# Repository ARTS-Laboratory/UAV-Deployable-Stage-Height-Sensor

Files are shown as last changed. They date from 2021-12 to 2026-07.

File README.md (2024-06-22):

# UAV-Deployable-Stage-Height-Sensor
UAV Deployable Stage Height Sensor with Electro-permanent Magnet Docking Mechanism

<p align="center">
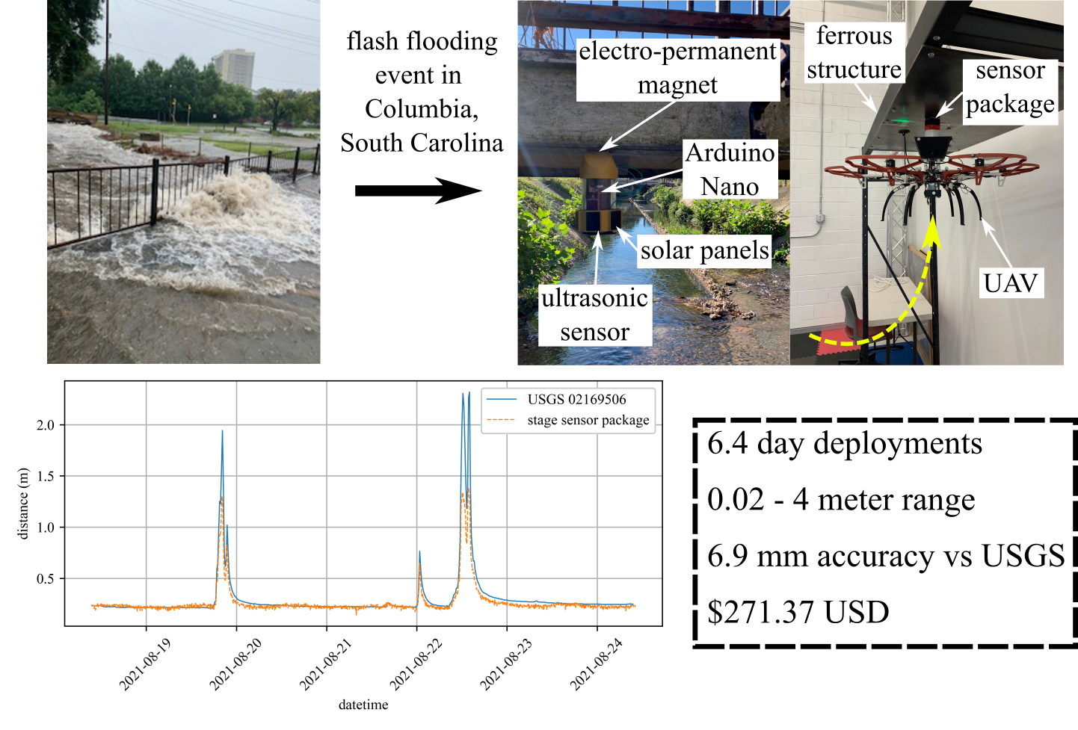
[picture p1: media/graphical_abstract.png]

</p>
<p align="center">
Figure 1: Drone delivering a sensor package underneath a structure.
</p>

## V0
1. Data logging saved onto SD card
2. Battery monitoring
3. Solar load sharing
4. Measures stage, temperature, pressure, humidity
5. EPM with wireless toggling to attach under structures

## V1 (projected)
1. Adaptive sampling algorithm
2. Wireless data transfer with GUI
3. Camera integration

## Licensing and Citation

[][cc-by-sa]

This work is licensed under a
[Creative Commons Attribution-ShareAlike 4.0 International License][cc-by-sa].

[cc-by-sa]: http://creativecommons.org/licenses/by-sa/4.0/
[cc-by-sa-image]: https://licensebuttons.net/l/by-sa/4.0/88x31.png
[cc-by-sa-shield]: https://img.shields.io/badge/License-CC%20BY--SA%204.0-lightgrey.svg

Cite as:

@Misc{ARTSLabUavDeployableStage,     
  author = {{ARTS-L}ab},  
  howpublished = {GitHub},  
  title  = {{UAV} Deployable Stage Height Sensor}, 
  groups = {{ARTS-L}ab},    
  url    = {https://github.com/ARTS-Laboratory/UAV-Deployable-Stage-Height-Sensor},   
}

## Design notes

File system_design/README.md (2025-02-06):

# System Design
Hardware variations named after coastal towns and cities in South Carolina

## Georgetown
Battery-powered ultrasonic sensor

## Charleston
Battery and solar panel-powered ultrasonic sensor

## Beaufort
Wireless communication in addition to battery and solar panel-powered ultrasonic sensor

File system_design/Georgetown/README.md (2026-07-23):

# Georgetown
UAV deployable sensor package for measuring water height. This document lists the updates made to the sensor pacakge over time.
## V0.1
1. Oldest version
2. Basic datalogger setup with modular RTC and SD card
3. Accelerometer integrated into daughter board

## V0.2
1. Teensy 4.0 microcontroller
2. Added environmental sensor

## V0.3
1. Teensy 4.0 or Arduino Nano microcontroller
2. Added DC current sensor

## V0.4
1. Arduino Nano microcontroller
2. Magnet power control circuit on daughter board
3. No accelerometer on daughter board
4. Solar panel load sharing on daughter board

## V0.5
1. Major CAD and PCB update from V0.4
2. Microcontroller : Arduino Nano
3. Solar panels moved to the bottom of the sensor package
4. BMS added to manage solar load sharing in main PCB, daughter PCB eliminated
5. Uses dynamic sleep interval depending on battery voltage level
6. Uses permanent magnet to attach to steel structures
7. Easy sliding water-proof clear tube

## V0.5.1
1. Minor design updates in PCB from V0.5.

## V0.5.2 (present version)
1. Major power electronics update from V0.5.1
2. Uses Mosfet based switching to turn off device during sleep. Wakes up using RTC interrupt. Resulting in very low power consumption and longer deployment time.
3. Sensing features: Water level distance from sensor, Humidity, temperature, pressure, battery voltage (recorded against RTC time)

## V0.6 (Proposed)
1.  Back to being UAV deployable using [this system](https://github.com/ARTS-Laboratory/UAV-Understructure-Sensor-Deployment-and-Recovery-System).
2. Uses module that has [single ultra sound transducer](https://cdn.shopify.com/s/files/1/0550/8091/0899/files/11832.pdf?v=1726578772) to lower current consumption.

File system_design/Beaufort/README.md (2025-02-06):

# Beaufort
Wireless communication in addition to battery and solar panel-powered ultrasonic sensor

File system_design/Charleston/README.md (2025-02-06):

# Charleston
Battery and solar panel-powered ultrasonic sensor

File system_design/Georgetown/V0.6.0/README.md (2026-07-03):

# UAV Rapidly-Deployable Stage Sensor with Permanent Magnet Docking Mechanism for Flood Monitoring in Undersampled Watersheds
## Deployment note
* Do not plug or unplug the SD card while power is on. Swtich must be turned to the off position to plug/unplug the SD card. 
## Fully assembled sensor package
<p align="center">

</p>

## System diagram
<p align="center">

</p>

## V0.5 PCB Top side
<p align="center">

</p>

## V0.5 PCB Bottom side
<p align="center">

</p>

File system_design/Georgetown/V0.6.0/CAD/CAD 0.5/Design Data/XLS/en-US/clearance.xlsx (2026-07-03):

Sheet: Ansi Unified Screw Threads
I | Sort Order -1
Fastener Type | Size | Shaft Diameters |  |  | Head Dimensions
 |  | Close | Normal | Loose | Diameter | Depth/Angle | Head Type
Flat Head Machine Screw (82) | #0 | 0.0635 | 0.07 | 0.073 | 0.119 | 82 | 2
Flat Head Machine Screw (82) | #1 | 0.076 | 0.081 | 0.089 | 0.146 | 82 | 2
Flat Head Machine Screw (82) | #2 | 0.089 | 0.096 | 0.1065 | 0.172 | 82 | 2
Flat Head Machine Screw (82) | #3 | 0.104 | 0.11 | 0.12 | 0.199 | 82 | 2
Flat Head Machine Screw (82) | #4 | 0.116 | 0.1285 | 0.136 | 0.225 | 82 | 2
Flat Head Machine Screw (82) | #5 | 0.1285 | 0.136 | 0.154 | 0.252 | 82 | 2
Flat Head Machine Screw (82) | #6 | 0.144 | 0.1495 | 0.1695 | 0.279 | 82 | 2
Flat Head Machine Screw (82) | #8 | 0.1695 | 0.177 | 0.1935 | 0.332 | 82 | 2
Flat Head Machine Screw (82) | #10 | 0.196 | 0.201 | 0.221 | 0.385 | 82 | 2
Flat Head Machine Screw (82) | #12 | 0.221 | 0.228 | 0.246 | 0.438 | 82 | 2
Flat Head Machine Screw (82) | 1/4 | 0.257 | 0.266 | 0.2812 | 0.507 | 82 | 2
Flat Head Machine Screw (82) | 5/16 | 0.323 | 0.332 | 0.3437 | 0.635 | 82 | 2
Flat Head Machine Screw (82) | 3/8 | 0.386 | 0.397 | 0.4062 | 0.762 | 82 | 2
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

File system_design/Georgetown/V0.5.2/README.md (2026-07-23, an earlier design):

# UAV Rapidly-Deployable Stage Sensor with Permanent Magnet Docking Mechanism for Flood Monitoring in Undersampled Watersheds
## Deployment note
* Do not plug or unplug the SD card while power is on. Swtich must be turned to the off position to plug/unplug the SD card. 
## Fully assembled sensor package
<p align="center">

</p>

## System diagram
<p align="center">
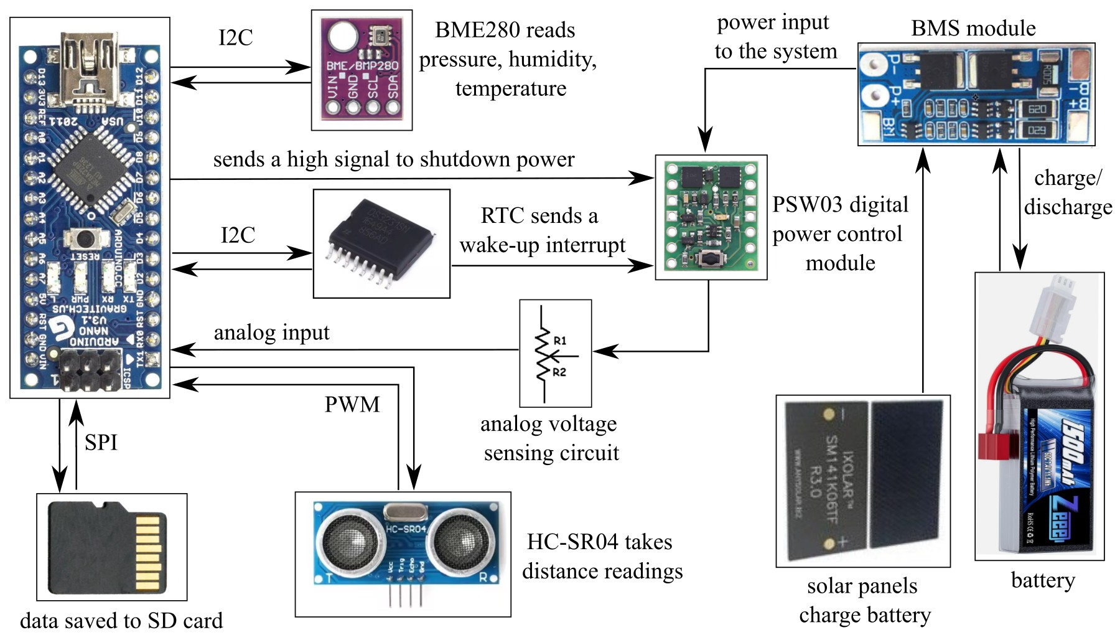
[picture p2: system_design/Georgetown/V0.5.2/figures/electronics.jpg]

</p>

## V0.5 PCB Top side
<p align="center">

</p>

## V0.5 PCB Bottom side
<p align="center">

</p>

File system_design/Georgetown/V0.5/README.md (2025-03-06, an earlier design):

# UAV Rapidly-Deployable Stage Sensor with Permanent Magnet Docking Mechanism for Flood Monitoring in Undersampled Watersheds

<p align="center">
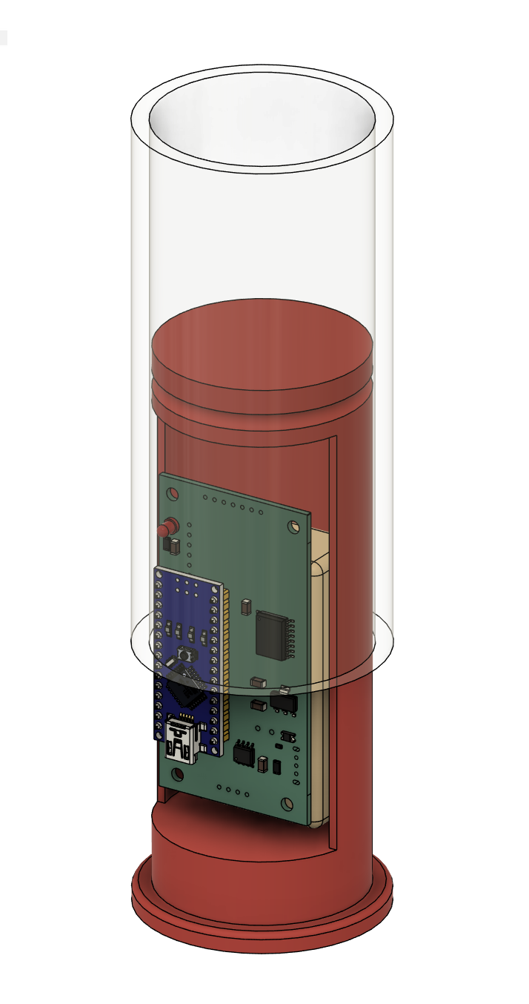
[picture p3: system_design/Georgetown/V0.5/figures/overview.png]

</p>

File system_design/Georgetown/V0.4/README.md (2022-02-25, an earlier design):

# UAV Rapidly-Deployable Stage Sensor with Electro-permanent Magnet Docking Mechanism for Flood Monitoring in Undersampled Watersheds

<p align="center">

</p>

## bill of materials
A complete bill of materials, with specifications for the base package, solar add-on module, and EPM add-on module

## CAD
STL and F3D files of 3D printed parts 

## code
Calibration and data collection codes

## EDA
KiCAD schematics and PCB layouts of main and daughter boards

## figures
SVG and PDF files of all figures presented in the work

## testing_data
Data from benchtop and field tests

## data_headers.csv
Example data headers for csv file generated by data_collection.ino

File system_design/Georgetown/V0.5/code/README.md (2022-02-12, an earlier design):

## clock_calibration
- calibrates the DS3231 to compiling time or a user defined time

## data_collection
- main program for base package with serial communication

## EPM_data_collection
- main program for EPM package acting as receiver

## magnet_toggle
- uses serial commands to toggle EPM on and off

## rf_controller
- configures a transmitter for the package with the RF controller PCB

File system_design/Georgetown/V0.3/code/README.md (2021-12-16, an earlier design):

## USS5_x
1. Compatible with Arduino Nano only

## USS5_asa
1. Sensor code with adaptive sampling algorithm integrated

## USS5_seconds
1. Sensor code with fixed 5 second intervals of sleep, used for debugging

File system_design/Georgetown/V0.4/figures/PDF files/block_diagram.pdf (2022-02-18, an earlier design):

MCU
Arduino
Nano

real-time
clock
DS3231

Li+
coin cell

ultrasonic sensor
HCSR04

onboard
memory
micro SD

wireless
communication
nRF24L01+
electropermanet
magnet
EPM V3 R5C

environmental
sensor
BME280

5V
regulator

current sensor
INA219

LiPo battery
Socokin 7.4V 1500 mAH

magnet power
control circuit

I2C

SPI

PWM

daughter board

main board

PWM

interrupt

interrupt

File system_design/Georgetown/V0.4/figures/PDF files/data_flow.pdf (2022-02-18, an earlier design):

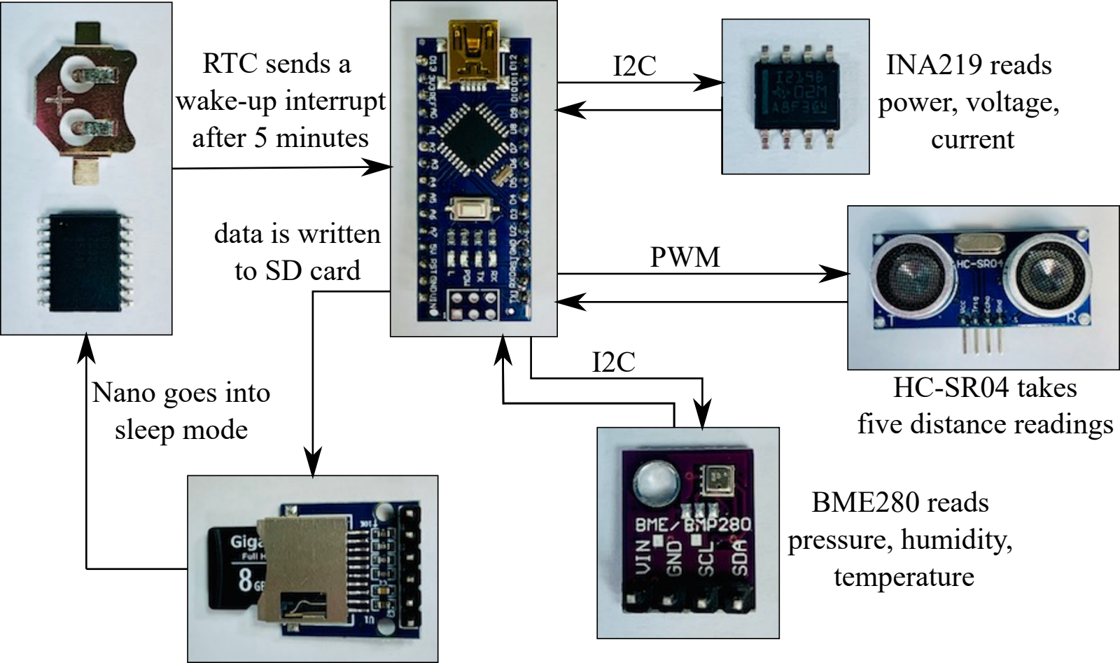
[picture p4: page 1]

RTC sends a
wake-up interrupt
after 5 minutes

INA219 reads
power, voltage,
current

HC-SR04 takes
five distance readings

BME280 reads
pressure, humidity,
temperature

data is written
to SD card

Nano goes into
sleep mode

I2C

PWM

I2C

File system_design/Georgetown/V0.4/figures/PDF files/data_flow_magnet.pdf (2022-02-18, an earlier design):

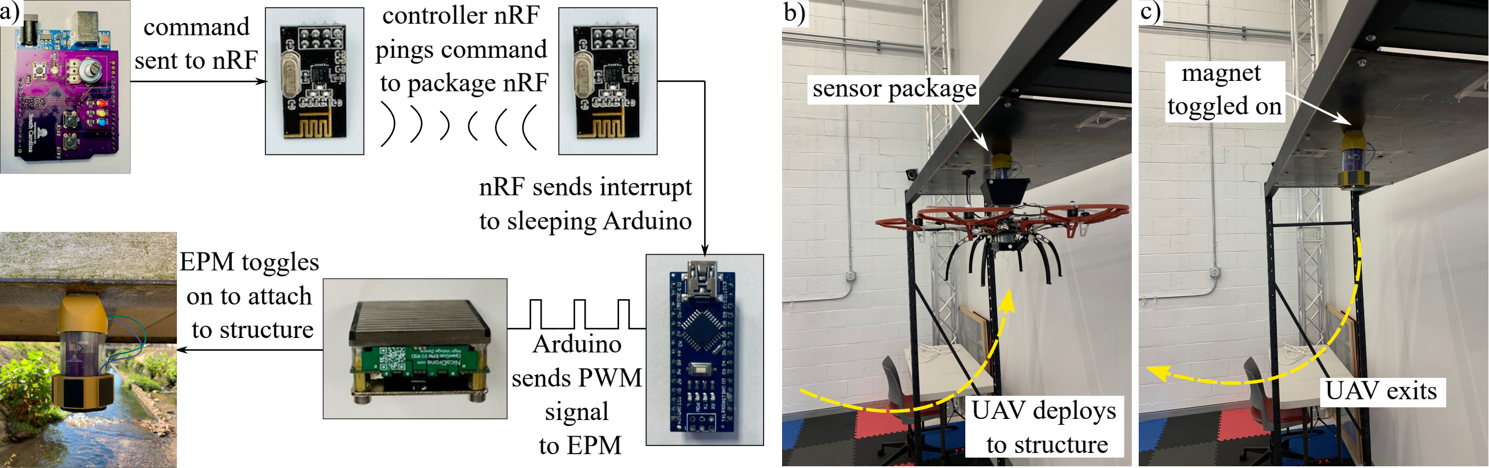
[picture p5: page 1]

command
sent to nRF

EPM toggles
on to attach
to structure | Arduino
| sends PWM
| signal
| to EPM

nRF sends interrupt
to sleeping Arduino

controller nRF
pings command
to package nRF

UAV exits

magnet
toggled on

UAV deploys
to structure

sensor package

a) | b) | c)

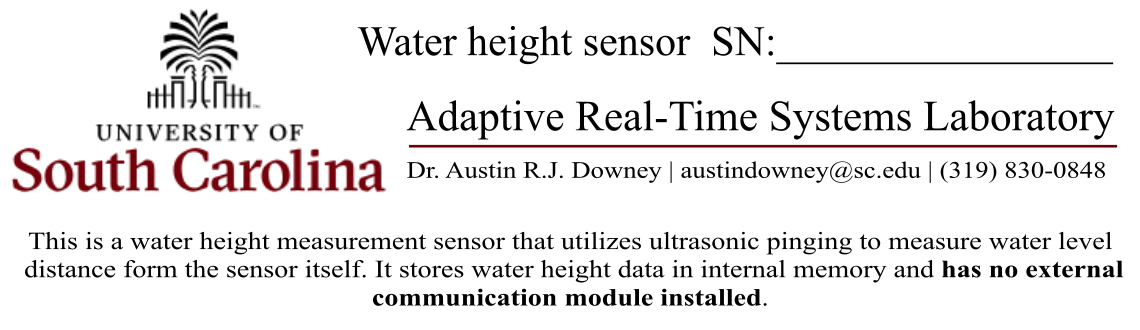
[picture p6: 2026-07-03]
system_design/Georgetown/V0.6.0/Sticker label/USC label.png

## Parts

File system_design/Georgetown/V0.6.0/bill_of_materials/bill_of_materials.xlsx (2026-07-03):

Designator | Component | Amount | Individual Cost | Total Cost | Vendor 1 | Vendor 2 | Vendor 3 | Vendor 4 | Vendor 5 | Vendor 6
Arduino Nano | Arduino Nano | 1 | 25.7 | 25.7 | https://store-usa.arduino.cc/products/arduino-nano?gad_source=1 | https://www.digikey.com/en/products/detail/arduino/A000005/2638989?gclsrc=aw.ds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 | https://www.ebay.com/itm/254630577493?chn=ps&google_free_listing_action=view_item&gQT=2
Micro SD card slot/tray | 112J-TDAR-R01 | 1 | 2.52 | 2.52 | https://www.digikey.com/en/products/detail/attend-technology/112J-TDAR-R01/17634680 | https://www.ebay.com/itm/235081679206?chn=ps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
NRF24L01+ | NRF24L01+ 2.4GHz Wireless RF Transceiver Module | 1 | 1.4 | 1.4 | https://www.amazon.com/Makerfire-Arduino-NRF24L01-Wireless-Transceiver/dp/B00O9O868G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 | https://www.digikey.com/en/products/detail/ai-thinker/NF-01-S/16688873?gclsrc=aw.ds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 | https://www.ebay.com/itm/185777140664?itmmeta=01JXJF02RJ2SD81DKBZE32WGPJ
DS3231 real-time clock | DS3231M+ | 1 | 11.96 | 11.96 | https://www.digikey.com/en/products/detail/analog-devices-inc-maxim-integrated/DS3231M/2402420 | https://www.mouser.com/ProductDetail/Analog-Devices-Maxim-Integrated/DS3231M%2b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
BME280 environmental sensor | BME280 | 1 | 5.26 | 5.26 | https://www.amazon.com/Onyehn-Temperature-Humidity-Barometric-Pressure/dp/B07KR24P6P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 | https://www.ebay.com/itm/223602242983?chn=ps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 | https://www.ebay.com/itm/183678893844?chn=ps&google_free_listing_action=view_item&gQT=2
INA219 current sensor | INA219BIDR | 1 | 2.03 | 2.03 | https://www.digikey.com/en/products/detail/texas-instruments/INA219BIDR/2426057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 | https://www.mouser.com/ProductDetail/Texas-Instruments/INA219BIDR?qs=1WmUhT/VMINyGsXNJcdD5Q%3D%3D&mgh=1&gQT=2 | https://www.ti.com/product/INA219/part-details/INA219BIDR
N42 permanent magnet | Neodymium Disc Magnet - 1 1/4" Dia x 3/8" Thi | 1 | 15.2 | 15.2 | https://www.kjmagnetics.com/dx46-neodymium-disc-magnet
Ultrasonic sensor | HC-SR04 | 1 | 5.25 | 5.25 | Ultrasonic Distance Sensor - 5V (HC-SR04) (https://www.sparkfun.com/ultrasonic-distance-sensor-hc-sr04.html) | https://www.digikey.com/en/products/detail/adafruit-industries-llc/3942/9658069?gclsrc=aw.ds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 | https://www.ebay.com/itm/192312930293?chn=ps&google_free_listing_action=view_item
2s 7.4V LiPo battery | Zeee 2S Lipo Battery 1500mAh 7.4V 60C with Deans Plug | 1 | 18 | 18 | https://zeeebattery.com/products/zeee-7-4v-60c-1500mah-2s-lipo-battery-deans-plug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 | https://www.ebay.com/itm/374993811392?chn=ps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 | https://www.digikey.com/en/products/detail/sparkfun-electronics/11855/5271297?gclsrc=aw.ds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
CR-1025 3V Li+ coin cell | CR-1025-ND | 1 | 1.09 | 1.09 | CR1025 Jauch Quartz | Battery Products | DigiKey (https://www.digikey.com/en/products/detail/jauch-quartz/CR1025/16399048) | https://www.ebay.com/itm/365610739537?chn=ps&google_free_listing_action=view_item
RTC coin cell holder | BK-870 | 1 | 0.58 | 0.58 | BK-870 MPD (Memory Protection Devices) | Battery Products | DigiKey (https://www.digikey.com/en/products/detail/mpd-memory-protection-devices/bk-870/3829737) | https://www.ebay.com/itm/133891769676?chn=ps&google_free_listing_action=view_item
Main PCB | Main board | 1 | 8.23 | 8.23 | https://oshpark.com/
Micro SD card | Gigastone 8GB 10-Pack Micro SD Card, Full HD Video 80MB/s Micro SDHC Class 10 | 1 | 8.24 | 8.24 | https://www.staples.com/centon-micro-8gb-sdhc-memory-card-uhs1-5-pack-s1-msdhu1-8g-5-b/product_24298979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 | https://www.staples.com/transcend-8gb-microsdhc-memory-card-class-10-ts8gusdhc10/product_IM1LK3226 | https://www.cdwg.com/product/transcend-flash-memory-card-8-gb-microsd/3181432?pfm=srh | https://www.cdwg.com/product/kingston-industrial-flash-memory-card-8-gb-microsdhc-uhs-i/6669743?pfm=srh | https://business.walmart.com/ip/Gigastone-8GB-Micro-SD-Card-FHD-Video-UHS-I-U1-Class-10-Surveillance-Security-Action-Cameras-Drone-Dash-Cams-5-Pack-5x8GB-GS-2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 | https://www.amazon.com/Gigastone-10-Pack-Surveillance-Security-Action/dp/B0876H387X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
Slide switch | 450301014042 | 1 | 2.03 | 2.03 | https://www.digikey.com/en/products/detail/w%C3%BCrth-elektronik/450301014042/5209104 | https://www.mouser.com/ProductDetail/Wurth-Elektronik/450301014042?qs=wr8lucFkNMW0uepaR4R%2Fww%3D%3D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
LED | L314ED | 1 | 0.2 | 0.2 | L314ED American Opto Plus LED | Optoelectronics | DigiKey Marketplace (https://www.digikey.com/en/products/detail/american-opto-plus-led/L314ED/13677700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) | https://www.lvelectronics.com/details/item?itemid=AOP%20L314ED
Resistors | RES SMD (4.7k) OHM 1% 1/4W 1206 | 7 | 0.1 | 0.7 | https://www.digikey.com/en/products/detail/bourns-inc/CR1206-JW-472ELF/3785627 | https://www.mouser.com/ProductDetail/Bourns/CR1206-JW-472ELF?qs=RBg%2F0eAeR6ePTxo24FnKCQ%3D%3D
Resistors | RES SMD (2K) OHM 1% 1/4W 1206 | 7 | 0.1 | 0.7 | https://www.digikey.com/en/products/detail/bourns-inc/CR1206-FX-2001ELF/2562846 | https://www.mouser.com/ProductDetail/KOA-Speer/RK73H2BLTD2001F?qs=iGskpj9dRIVPlylmUlAzCg%3D%3D
Resistors | RES SMD (1k) OHM 1% 1/4W 1206 | 7 | 0.1 | 0.7 | https://www.digikey.com/en/products/detail/bourns-inc/CR1206-FX-1001ELF/2562677 | https://www.mouser.com/ProductDetail/YAGEO/SR1206FR-071KL?qs=k2KEx2DUIRRzYfz4yJHffA%3D%3D
Shunt resistor | ERJ-8BSJR10V RES 0.1 OHM 5\% 1/2W 1206 | 1 | 0.34 | 0.34 | ERJ-8BSJR10V Panasonic Electronic Components | Resistors | DigiKey (https://www.digikey.com/en/products/detail/panasonic-electronic-components/ERJ-8BSJR10V/5647718) | https://www.mouser.com/ProductDetail/Panasonic/ERJ-8BSJR10V?qs=22lEN67Lqx5%2FgSl4VxUkKw%3D%3D
Schottky Diode | SD1206T020S1R0 | 1 | 0.39 | 0.39 | https://www.digikey.com/en/products/detail/kyocera-avx/SD1206T020S1R0/3749511 | https://www.mouser.com/ProductDetail/KYOCERA-AVX/SD1206T020S1R0?qs=jCA%252BPfw4LHaOj8Rzt48dmw%3D%3D
Capacitor 22uF | TAJA226K006RNJ | 1 | 0.41 | 0.41 | https://www.digikey.com/en/products/detail/kyocera-avx/TAJA226K006RNJ/1126793 | https://www.mouser.com/ProductDetail/KYOCERA-AVX/TAJA226K006RNJ?qs=QtLZGLLAmDbrbL0%252BYUNp1A%3D%3D
Capacitor 10uF | ECE-A1EKS100B | 1 | 0.26 | 0.26 | https://www.digikey.com/en/products/detail/panasonic-electronic-components/ECE-A1EKS100B/2689095 | https://www.mouser.com/ProductDetail/Panasonic/ECE-A1EKS100B?qs=rMMd5vBiahpNSBku%2FPA9KQ%3D%3D
Capacitors 0.1uF | C1206S104K5RACAUTO 0.1 uF 10% 50V Ceramic Capacitor X7R 1206 (3216 Metric) | 4 | 0.48 | 1.92 | C1206S104K5RACAUTO KEMET | Capacitors | DigiKey (https://www.digikey.com/en/products/detail/kemet/c1206s104k5racauto/10232834) | https://www.mouser.com/ProductDetail/KEMET/C1206S104K5RACAUTO?qs=ds50AKTGxA9C%252BOGFjvBCPg%3D%3D
5V regulator | MIC5239-5.0YS-TR | 1 | 3.58 | 3.58 | MIC5239-5.0YS-TR Microchip Technology | Integrated Circuits (ICs) | DigiKey (https://www.digikey.com/en/products/detail/microchip-technology/mic5239-5-0ys-tr/2346595) | https://www.microchipdirect.com/product/MIC5239-5.0YS-TR | https://www.mouser.com/ProductDetail/Microchip-Technology/MIC5239-5.0YS-TR?qs=U6T8BxXiZAVR02O8mv9RNQ%3D%3D
PVC pipe | Schedule 40 Clear Pipe, Non-threaded | 4 inch | 2.9 | 2.9 | https://www.grainger.com/product/1AAZ8?gclsrc=aw.ds&gad_source=1&gad_campaignid=21375667808
Female HC-SR04 connector | SSA-104-W-T | 1 | 0.91 | 0.91 | SSA-104-W-T Samtec Inc. | Connectors, Interconnects | DigiKey (https://www.digikey.com/en/products/detail/samtec-inc/ssa-104-w-t/1105908) | https://www.samtec.com/products/ssa-104-w-t
BMS | HX-2S-JH10 | 1 | 2.15 | 2.15 | https://www.ebay.com/itm/122175451692?_skw=2s+7.4v+bms&itmmeta=01JC4ZYQC0WA4Q7FSXJ13Q3MD7 | https://www.ebay.com/itm/386425796959?itmmeta=01JX0567N9MHM61DNDR0TWAKGV
2.54mm JST 3 pin | B3B-XH-A | 1 | 0.13 | 0.13 | https://www.digikey.com/en/products/detail/jst-sales-america-inc/B3B-XH-A/1651046?gad_source=1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 | https://www.ebay.com/itm/135516167050?_skw=B3B-XH-A&itmmeta=01JXJN27KW3SV3ZA95H65390XD
Solar panels | SM141K06TF | 9 | 7.39 | 66.51 | https://www.digikey.com/en/products/detail/anysolar-ltd/SM141K06TF/14311398
M2 nut |  | 2 | 0.01 | 0.02
M2 bolt |  | 2 | 0.073 | 0.14 | https://www.grainger.com/product/Machine-Screws-M2x0-40-Thread-6GY22?
O-Rings |  | 1 | 0.26 | 4.7 | https://www.grainger.com/product/O-Ring-Buna-N-41KW27
Total Cost | 194.15

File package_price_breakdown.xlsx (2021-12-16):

Name | Amazon Price | Digikey Price | Other supplier | Water height sensor | Rain gauge | Accelerometer | Dissolved solids sensor | Camera package | Spike
Arduino Nano | $3.60 | $22.00 |  | X | X |  | X
Arduino Teensy | $14.70 | $24.38 |  |  |  | X
Real Time Clock |  | $6.92 |  | X | X | X | X
Micro SD reader |  | $1.09 |  | X | X | X | X
NRF Chip |  | $1.19 |  | X | X | X | X
INA219 current sensor |  | $2.41 |  | X | X |  | X
5V regulator |  | $2.79 |  | X | X
PNP transistor |  | $0.37 |  | X | X
NPN Transistor |  | $0.36 |  | X | X
RTC battery and holder |  | $1.28 |  | X | X |  | X
90 deg rails | $1.11 | $0.93 |  | X | X | X | X
Resistors |  | $0.01 |  | X | X | X | X
Switch | $0.62 |  |  | X | X | X | X
LED |  | $0.02 |  | X | X | X | X
NicoDrone Magnet |  |  | $159.99 | X | X | X
LiPo Battery | $12.49 |  |  | X | X | X | X
2" PVC |  |  | $0.75 | X | X | X | X
Solar panels |  | $5.71 |  | X | X |  | X
Printed PLA parts |  |  |  | X | X | X | X
HC-SR04 Ultrasonic sensor | $4.95 | $3.95 |  | X
SCA 3300 Accelerometer |  | $33.56 |  |  |  | X
Dissolved solids breakout board | $13.99 | $13.03 |  |  |  |  | X
BME280 Environmental Sensor | $4.25 | $14.25 |  | X | X | X
Dean's Connector | $0.50 | $0.95 |  | X | X | X | X
Main PCB |  |  | $6.28 | X | X | X | X
Daughter PCB |  |  | $4.15 | X | X | X
FLIR blackfly
3D printer
Machining costs
Total Price per Package: |  |  |  | $230.12 | $226.17 | #REF! | $51.58

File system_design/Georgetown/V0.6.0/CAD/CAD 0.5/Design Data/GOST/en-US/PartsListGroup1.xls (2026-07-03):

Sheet: Лист 1
Инв. № подл |  |  |  | Подп. и дата | Взам. инв. № | Инв. № дубл. |  |  | Подп. и дата
Формат | Зона | Поз. | Обозначение |  |  |  | Наименование |  |  |  |  |  | Кол. на исполнение
 |  |  |  |  |  |  |  |  |  |  |  | Лит.
 |  |  |  |  |  |  |  |  |  |  |  | Код
 |  |  |  |  |  |  |  | Изм. | Лист | № докум | Подпись |  | Дата
 |  |  |  |  |  |  |  | Разраб.
 |  |  |  |  |  |  |  | Пров.
 |  |  |  |  |  |  |  | Н.контр
 |  |  |  |  |  |  |  | Утв.
 |  |  |  |  |  |  |  |  |  |  |  |  |  | Копировал

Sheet: Лист 2
Инв. № подл |  |  |  | Подп. и дата | Взам. инв. № | Инв. № дубл. |  |  | Подп. и дата
Формат | Зона | Поз. | Обозначение |  |  |  | Наименование |  |  |  |  | Кол. на исполнение
 |  |  |  |  |  |  |  | Изм. | Лист | № докум. | Подп. | Дата
 |  |  |  |  |  |  |  |  |  |  |  |  | Копировал
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

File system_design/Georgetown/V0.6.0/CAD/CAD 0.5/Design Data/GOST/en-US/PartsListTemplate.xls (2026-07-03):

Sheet: Лист 1
 | Формат | Зона |  | Поз. |  | Обозначение |  |  |  | Наименование |  |  |  | Кол. | Приме-чание
Подп. и дата
Инв. № дубл.
Взам. инв. №
Подп. и дата
 | Изм. |  | Лист |  | № докум |  | Подпись | Дата
Инв. № подл | Разраб. |  |  |  |  |  |  |  |  |  | Литера |  | Лист |  |  | Листов
 | Пров.
 | Н.контр
 | Утв.
 |  |  |  |  |  |  |  |  | Копировал |  |  | Формат А4

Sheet: Лист 2
 | Формат | Зона |  | Поз. |  | Обозначение |  |  |  | Наименование |  | Кол. | Приме-чание
Подп. и дата
Инв. № дубл.
Взам. инв. №
Подп. и дата
Инв. № подл
 | Изм. |  | Лист |  | № докум. |  | Подп. |  | Дата
 |  |  |  |  |  |  |  | Копировал |  |  | Формат А4
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

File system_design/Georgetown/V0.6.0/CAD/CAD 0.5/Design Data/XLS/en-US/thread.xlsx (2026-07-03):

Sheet: Inch Tapping Threads
I Q X | Inch Tapping Threads |  | Sort Order - 5 |  | External |  |  |  |  |  |  | Internal
 |  |  |  |  |  | Major Dia |  | Pitch Dia |  | Minor Dia |  |  | Minor Dia |  | Pitch Dia |  | Major Dia |  | Tap Drill
Size | Size Suffix | Thread Designation | Custom Thread Designation | TPI | Class | Max | Min | Max | Min | Max | Min | Class | Min | Max | Min | Max | Min | Max | Basic
0.0600 |  | 0-48 | 0-48 | 48 | 2B | 0.0600 | 0.0540 | 0.0480 | 0.0435 | 0.0360 | 0.0330
0.0730 |  | 1-42 | 1-42 | 42 | 2B | 0.0750 | 0.0690 | 0.0620 | 0.0575 | 0.0490 | 0.0460
0.0860 |  | 2-32 | 2-32 | 32 | 2B | 0.0880 | 0.0820 | 0.0760 | 0.0710 | 0.0640 | 0.0600
0.0990 |  | 3-28 | 3-28 | 28 | 2B | 0.1010 | 0.0950 | 0.0880 | 0.0830 | 0.0750 | 0.0710
0.1120 |  | 4-24 | 4-24 | 24 | 2B | 0.1140 | 0.1080 | 0.1000 | 0.0950 | 0.0860 | 0.0820
0.1250 |  | 5-20 | 5-20 | 20 | 2B | 0.1300 | 0.1230 | 0.1120 | 0.1065 | 0.0940 | 0.0900
0.1380 |  | 6-20 | 6-20 | 20 | 2B | 0.1390 | 0.1320 | 0.1215 | 0.1155 | 0.1040 | 0.0990
0.1510 |  | 7-19 | 7-19 | 19 | 2B | 0.1540 | 0.1470 | 0.1345 | 0.1280 | 0.1150 | 0.1090
0.1640 |  | 8-18 | 8-18 | 18 | 2B | 0.1660 | 0.1590 | 0.1440 | 0.1375 | 0.1220 | 0.1160
0.1900 |  | 10-16 | 10-16 | 16 | 2B | 0.1890 | 0.1820 | 0.1650 | 0.1585 | 0.1410 | 0.1350
0.2160 |  | 12-14 | 12-14 | 14 | 2B | 0.2150 | 0.2080 | 0.1895 | 0.1825 | 0.1640 | 0.1570
0.2420 |  | 14-14 | 14-14 | 14 | 2B | 0.2410 | 0.2340 | 0.2130 | 0.2060 | 0.1850 | 0.1780
0.2500 |  | 1/4-14 | 1/4-14 | 14 | 2B | 0.2460 | 0.2370 | 0.2190 | 0.2110 | 0.1920 | 0.1850
0.3125 |  | 5/16-12 | 5/16-12 | 12 | 2B | 0.3150 | 0.3060 | 0.2795 | 0.2710 | 0.2440 | 0.2360
0.3750 |  | 3/8-12 | 3/8-12 | 12 | 2B | 0.3800 | 0.3710 | 0.3445 | 0.3350 | 0.3090 | 0.2990
0.4375 |  | 7/16-10 | 7/16-10 | 10 | 2B | 0.4400 | 0.4290 | 0.3995 | 0.3890 | 0.3590 | 0.3490
0.5000 |  | 1/2-10 | 1/2-10 | 10 | 2B | 0.5040 | 0.4930 | 0.4635 | 0.4530 | 0.4230 | 0.4130

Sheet: Metric Forming Screw Threads
M P X | Metric Forming Screw Threads |  | Sort Order - 6 |  | External |  |  |  |  |  |  | Internal
 |  |  |  |  |  | Major Dia |  | Pitch Dia |  | Minor Dia |  |  | Minor Dia |  | Pitch Dia |  | Major Dia |  | Tap Drill
Size | Size Suffix | Thread Designation | Custom Thread Designation | Pitch | Class | Max | Min | Max | Min | Max | Min | Class | Min | Max | Min | Max | Min | Max | Basic
1.5 |  | 1.5x0.5 | 1.5x0.5 | 0.5 | 6g | 1.520 | 1.380 | 1.215 | 1.110 | 0.910 | 0.840
1.5 |  | ST1.5x0.5 | ST1.5x0.5 | 0.5 | 6g | 1.520 | 1.380 | 1.215 | 1.110 | 0.910 | 0.840
1.9 |  | 1.9x0.6 | 1.9x0.6 | 0.6 | 6g | 1.900 | 1.760 | 1.570 | 1.465 | 1.240 | 1.170
1.9 |  | ST1.9x0.6 | ST1.9x0.6 | 0.6 | 6g | 1.900 | 1.760 | 1.570 | 1.465 | 1.240 | 1.170
2.2 |  | 2.2x0.8 | 2.2x0.8 | 0.8 | 6g | 2.240 | 2.100 | 1.935 | 1.810 | 1.630 | 1.520
2.2 |  | ST2.2x0.8 | ST2.2x0.8 | 0.8 | 6g | 2.240 | 2.100 | 1.935 | 1.810 | 1.630 | 1.520
2.6 |  | 2.6x0.9 | 2.6x0.9 | 0.9 | 6g | 2.570 | 2.430 | 2.235 | 2.115 | 1.900 | 1.800
2.6 |  | ST2.6x0.9 | ST2.6x0.9 | 0.9 | 6g | 2.570 | 2.430 | 2.235 | 2.115 | 1.900 | 1.800
2.9 |  | 2.9x1 | 2.9x1 | 1 | 6g | 2.900 | 2.760 | 2.540 | 2.420 | 2.180 | 2.080
2.9 |  | 2.9x1.1 | 2.9x1.1 | 1.1 | 6g | 2.900 | 2.760 | 2.540 | 2.420 | 2.180 | 2.080
2.9 |  | ST2.9x1.1 | ST2.9x1.1 | 1.1 | 6g | 2.900 | 2.760 | 2.540 | 2.420 | 2.180 | 2.080
2.9 |  | 2.9x1.3 | 2.9x1.3 | 1.3 | 6g | 2.900 | 2.720 | 2.540 | 2.355 | 1.890 | 1.700
2.9 |  | 2.9x1.4 | 2.9x1.4 | 1.4 | 6g | 2.900 | 2.720 | 2.340 | 2.175 | 1.780 | 1.630
3.3 |  | 3.3x1.3 | 3.3x1.3 | 1.3 | 6g | 3.300 | 3.120 | 2.795 | 2.665 | 2.290 | 2.210
3.3 |  | ST3.3x1.3 | ST3.3x1.3 | 1.3 | 6g | 3.300 | 3.120 | 2.795 | 2.665 | 2.290 | 2.210
3.5 |  | 3.5x1.3 | 3.5x1.3 | 1.3 | 6g | 3.530 | 3.350 | 3.085 | 2.930 | 2.640 | 2.510
3.5 |  | ST3.5x1.3 | ST3.5x1.3 | 1.3 | 6g | 3.530 | 3.350 | 3.085 | 2.930 | 2.640 | 2.510
3.5 |  | 3.5x1.6 | 3.5x1.6 | 1.6 | 6g | 3.530 | 3.350 | 2.920 | 2.755 | 2.310 | 2.160
3.5 |  | 3.5x3.2 | 3.5x3.2 | 3.2 | 6g | 3.530 | 3.310 | 2.800 | 2.600 | 2.070 | 1.890
3.9 |  | 3.9x1.3 | 3.9x1.3 | 1.3 | 6g | 3.910 | 3.730 | 3.415 | 3.250 | 2.920 | 2.770
3.9 |  | ST3.9x1.3 | ST3.9x1.3 | 1.3 | 6g | 3.910 | 3.730 | 3.415 | 3.250 | 2.920 | 2.770
3.9 |  | 3.9x1.6 | 3.9x1.6 | 1.6 | 6g | 3.910 | 3.730 | 3.300 | 3.135 | 2.690 | 2.540
3.9 |  | 3.9x3.2 | 3.9x3.2 | 3.2 | 6g | 3.910 | 3.690 | 3.180 | 2.980 | 2.450 | 2.270
4.2 |  | 4.2x1.4 | 4.2x1.4 | 1.4 | 6g | 4.220 | 4.040 | 3.660 | 3.495 | 3.100 | 2.950
4.2 |  | ST4.2x1.4 | ST4.2x1.4 | 1.4 | 6g | 4.220 | 4.040 | 3.660 | 3.495 | 3.100 | 2.950
4.2 |  | 4.2x1.6 | 4.2x1.6 | 1.6 | 6g | 4.220 | 4.040 | 3.610 | 3.445 | 3.000 | 2.850
4.2 |  | 4.2x3.2 | 4.2x3.2 | 3.2 | 6g | 4.220 | 4.000 | 3.380 | 3.180 | 2.540 | 2.360
4.8 |  | 4.8x1.6 | 4.8x1.6 | 1.6 | 6g | 4.800 | 4.620 | 4.190 | 4.025 | 3.580 | 3.430
4.8 |  | ST4.8x1.6 | ST4.8x1.6 | 1.6 | 6g | 4.800 | 4.620 | 4.190 | 4.025 | 3.580 | 3.430
4.8 |  | 4.8x1.8 | 4.8x1.8 | 1.8 | 6g | 4.800 | 4.620 | 4.065 | 3.885 | 3.330 | 3.150
4.8 |  | 4.8x3.2 | 4.8x3.2 | 3.2 | 6g | 4.800 | 4.580 | 3.960 | 3.760 | 3.120 | 2.940
5.5 |  | 5.5x1.8 | 5.5x1.8 | 1.8 | 6g | 5.460 | 5.280 | 4.815 | 4.635 | 4.170 | 3.990
5.5 |  | ST5.5x1.8 | ST5.5x1.8 | 1.8 | 6g | 5.460 | 5.280 | 4.815 | 4.635 | 4.170 | 3.990
6.3 |  | 6.3x1.8 | 6.3x1.8 | 1.8 | 6g | 6.250 | 6.030 | 5.565 | 5.365 | 4.880 | 4.700
6.3 |  | ST6.3x1.8 | ST6.3x1.8 | 1.8 | 6g | 6.250 | 6.030 | 5.565 | 5.365 | 4.880 | 4.700
8.0 |  | 8x2.1 | 8x2.1 | 2.1 | 6g | 8.000 | 7.780 | 7.100 | 6.885 | 6.200 | 5.990
8.0 |  | ST8x2.1 | ST8x2.1 | 2.1 | 6g | 8.000 | 7.780 | 7.100 | 6.885 | 6.200 | 5.990
9.5 |  | 9.5x2.1 | 9.5x2.1 | 2.1 | 6g | 9.650 | 9.430 | 8.750 | 8.510 | 7.850 | 7.590
9.5 |  | ST9.5x2.1 | ST9.5x2.1 | 2.1 | 6g | 9.650 | 9.430 | 8.750 | 8.510 | 7.850 | 7.590

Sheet: ISO Pipe Threads
M Q | ISO Pipe Threads |  | Sort Order - 9 |  | External |  |  |  |  |  |  | Internal
 |  |  |  |  |  | Major Dia |  | Pitch Dia |  | Minor Dia |  |  | Minor Dia |  | Pitch Dia |  | Major Dia |  | Tap Drill | Thread Depth | Thread Runouts
Size | Size Suffix | Thread Designation | Custom Thread Designation | TPI | Class | Max | Min | Max | Min | Max | Min | Class | Min | Max | Min | Max | Min | Max | Basic
7.723 |  | G7.723x0.907 | G 1/16 | 28 | A | 7.723 | 7.509 | 7.142 | 7.035 | 6.561 |  |  | 6.561 | 6.834 | 7.142 | 7.249 | 7.723 |  | 1.5875 | 15.446 | 4.5000
7.723 |  | G7.723x0.907 | G 1/16 | 28 | B | 7.723 | 7.509 | 7.142 | 6.928 | 6.561
9.728 |  | G9.728x0.907 | G 1/8 | 28 | A | 9.728 | 9.514 | 9.147 | 9.040 | 8.566 |  |  | 8.566 | 8.848 | 9.147 | 9.254 | 9.728 |  | 3.1750 | 19.456 | 4.5000
9.728 |  | G9.728x0.907 | G 1/8 | 28 | B | 9.728 | 9.514 | 9.147 | 8.933 | 8.566
13.157 |  | G13.157x1.337 | G 1/4 | 19 | A | 13.157 | 12.907 | 12.301 | 12.176 | 11.445 |  |  | 11.445 | 11.89 | 12.301 | 12.426 | 13.157 |  | 6.3500 | 26.314 | 6.5000
13.157 |  | G13.157x1.337 | G 1/4 | 19 | B | 13.157 | 12.907 | 12.301 | 12.051 | 11.445
16.662 |  | G16.662x1.337 | G 3/8 | 19 | A | 16.662 | 16.412 | 15.806 | 15.681 | 14.950 |  |  | 14.95 | 15.395 | 15.806 | 15.931 | 16.662 |  | 9.5250 | 33.324 | 6.5000
16.662 |  | G16.662x1.337 | G 3/8 | 19 | B | 16.662 | 16.412 | 15.806 | 15.556 | 14.950
20.955 |  | G20.955x1.814 | G 1/2 | 14 | A | 20.955 | 20.671 | 19.793 | 19.651 | 18.631 |  |  | 18.631 | 19.172 | 19.793 | 19.935 | 20.955 |  | 12.7000 | 41.910 | 8.5000
20.955 |  | G20.955x1.814 | G 1/2 | 14 | B | 20.955 | 20.671 | 19.793 | 19.509 | 18.631
22.911 |  | G22.911x1.814 | G 5/8 | 14 | A | 22.911 | 22.627 | 21.749 | 21.607 | 20.587 |  |  | 20.587 | 21.128 | 21.749 | 21.891 | 22.911 |  |  | 45.822 | 8.5000
22.911 |  | G22.911x1.814 | G 5/8 | 14 | B | 22.911 | 22.627 | 21.749 | 21.465 | 20.587
26.441 |  | G26.441x1.814 | G 3/4 | 14 | A | 26.441 | 26.157 | 25.279 | 25.137 | 24.117 |  |  | 24.117 | 24.658 | 25.279 | 25.421 | 26.441 |  | 15.8750 | 52.882 | 8.5000
26.441 |  | G26.441x1.814 | G 3/4 | 14 | B | 26.441 | 26.157 | 25.279 | 24.995 | 24.117
30.201 |  | G30.201x1.814 | G 7/8 | 14 | A | 30.201 | 29.917 | 29.039 | 28.897 | 27.877 |  |  | 27.877 | 28.418 | 29.039 | 29.181 | 30.201 |  | 22.2250 | 60.402 | 8.5000
30.201 |  | G30.201x1.814 | G 7/8 | 14 | B | 30.201 | 29.917 | 29.039 | 28.755 | 27.877
33.249 |  | G33.249x2.309 | G 1 | 11 | A | 33.249 | 32.889 | 31.770 | 31.590 | 30.291 |  |  | 30.291 | 30.931 | 31.77 | 31.95 | 33.249 |  | 25.4000 | 66.498 | 10.0000
33.249 |  | G33.249x2.309 | G 1 | 11 | B | 33.249 | 32.889 | 31.770 | 31.410 | 30.291
37.897 |  | G37.897x2.309 | G 1 1/8 | 11 | A | 37.897 | 37.537 | 36.418 | 36.238 | 34.939 |  |  | 34.939 | 35.579 | 36.418 | 36.598 | 37.897 |  | 28.5750 | 75.794 | 10.0000
37.897 |  | G37.897x2.309 | G 1 1/8 | 11 | B | 37.897 | 37.537 | 36.418 | 36.058 | 34.939
41.910 |  | G41.91x2.309 | G 1 1/4 | 11 | A | 41.910 | 41.550 | 40.431 | 40.251 | 38.952 |  |  | 38.952 | 39.592 | 40.431 | 40.611 | 41.910 |  | 31.7500 | 83.820 | 10.0000
41.910 |  | G41.91x2.309 | G 1 1/4 | 11 | B | 41.910 | 41.550 | 40.431 | 40.071 | 38.952
47.803 |  | G47.803x2.309 | G 1 1/2 | 11 | A | 47.803 | 47.443 | 46.324 | 46.144 | 44.845 |  |  | 44.845 | 45.485 | 46.324 | 46.504 | 47.803 |  | 38.1000 | 95.606 | 10.0000
47.803 |  | G47.803x2.309 | G 1 1/2 | 11 | B | 47.803 | 47.443 | 46.324 | 45.964 | 44.845
53.746 |  | G53.746x2.309 | G 1 3/4 | 11 | A | 53.746 | 53.386 | 52.267 | 52.087 | 50.788 |  |  | 50.788 | 51.428 | 52.267 | 52.447 | 53.746 |  | 44.4500 | 107.492 | 10.0000
53.746 |  | G53.746x2.309 | G 1 3/4 | 11 | B | 53.746 | 53.386 | 52.267 | 51.907 | 50.788
59.614 |  | G59.614x2.309 | G 2 | 11 | A | 59.614 | 59.254 | 58.135 | 57.955 | 56.656 |  |  | 56.656 | 57.296 | 58.135 | 58.315 | 59.614 |  | 50.8000 | 119.228 | 10.0000
59.614 |  | G59.614x2.309 | G 2 | 11 | B | 59.614 | 59.254 | 58.135 | 57.775 | 56.656
65.710 |  | G65.71x2.309 | G 2 1/4 | 11 | A | 65.710 | 65.276 | 64.231 | 64.014 | 62.752 |  |  | 62.752 | 63.392 | 64.231 | 64.448 | 65.710 |  | 57.1500 | 131.420 | 10.0000
65.710 |  | G65.71x2.309 | G 2 1/4 | 11 | B | 65.710 | 65.276 | 64.231 | 63.797 | 62.752
75.184 |  | G75.184x2.309 | G 2 1/2 | 11 | A | 75.184 | 74.750 | 73.705 | 73.488 | 72.226 |  |  | 72.226 | 72.866 | 73.705 | 73.922 | 75.184 |  |  | 150.368 | 10.0000
75.184 |  | G75.184x2.309 | G 2 1/2 | 11 | B | 75.184 | 74.750 | 73.705 | 73.271 | 72.226
81.534 |  | G81.534x2.309 | G 2 3/4 | 11 | A | 81.534 | 81.100 | 80.055 | 79.838 | 78.576 |  |  | 78.576 | 79.216 | 80.055 | 80.272 | 81.534 |  | 69.8500 | 163.068 | 10.0000
81.534 |  | G81.534x2.309 | G 2 3/4 | 11 | B | 81.534 | 81.100 | 80.055 | 79.621 | 78.576
87.884 |  | G87.884x2.309 | G 3 | 11 | A | 87.884 | 87.450 | 86.405 | 86.188 | 84.926 |  |  | 84.926 | 85.566 | 86.405 | 86.622 | 87.884 |  | 76.2000 | 175.768 | 10.0000
87.884 |  | G87.884x2.309 | G 3 | 11 | B | 87.884 | 87.450 | 86.405 | 85.971 | 84.926
100.330 |  | G100.33x2.309 | G 3 1/2 | 11 | A | 100.330 | 99.896 | 98.851 | 98.634 | 97.372 |  |  | 97.372 | 98.012 | 98.851 | 99.068 | 100.330 |  | 88.9000 | 200.660 | 10.0000
100.330 |  | G100.33x2.309 | G 3 1/2 | 11 | B | 100.330 | 99.896 | 98.851 | 98.417 | 97.372
113.030 |  | G113.03x2.309 | G 4 | 11 | A | 113.030 | 112.596 | 111.551 | 111.334 | 110.072 |  |  | 110.072 | 110.712 | 111.551 | 111.768 | 113.030 |  | 101.6000 | 226.060 | 10.0000
113.030 |  | G113.03x2.309 | G 4 | 11 | B | 113.030 | 112.596 | 111.551 | 111.117 | 110.072
125.730 |  | G125.73x2.309 | G 4 1/2 | 11 | A | 125.730 | 125.296 | 124.251 | 124.034 | 122.772 |  |  | 122.772 | 123.412 | 124.251 | 124.468 | 125.730 |  | 114.3000 | 251.460 | 10.0000
125.730 |  | G125.73x2.309 | G 4 1/2 | 11 | B | 125.730 | 125.296 | 124.251 | 123.817 | 122.772
138.430 |  | G138.43x2.309 | G 5 | 11 | A | 138.430 | 137.996 | 136.951 | 136.734 | 135.472 |  |  | 135.472 | 136.112 | 136.951 | 137.168 | 138.430 |  | 127.0000 | 276.860 | 10.0000
138.430 |  | G138.43x2.309 | G 5 | 11 | B | 138.430 | 137.996 | 136.951 | 136.517 | 135.472
151.130 |  | G151.13x2.309 | G 5 1/2 | 11 | A | 151.130 | 150.696 | 149.651 | 149.434 | 148.172 |  |  | 148.172 | 148.812 | 149.651 | 149.868 | 151.130 |  | 139.7000 | 302.260 | 10.0000
151.130 |  | G151.13x2.309 | G 5 1/2 | 11 | B | 151.130 | 150.696 | 149.651 | 149.217 | 148.172
163.830 |  | G163.83x2.309 | G 6 | 11 | A | 163.830 | 163.396 | 162.351 | 162.134 | 160.872 |  |  | 160.872 | 161.512 | 162.351 | 162.568 | 163.830 |  | 152.4000 | 327.660 | 10.0000
163.830 |  | G163.83x2.309 | G 6 | 11 | B | 163.830 | 163.396 | 162.351 | 161.917 | 160.872

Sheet: JIS Pipe Threads
M Q | JIS Pipe Threads |  | Sort Order -12 |  | External |  |  |  |  |  |  | Internal
 |  |  |  |  |  | Major Dia |  | Pitch Dia |  | Minor Dia |  |  | Minor Dia |  | Pitch Dia |  | Major Dia |  | Tap Drill | Thread Depth | Thread Runouts
Size | Size Suffix | Thread Designation | Custom Thread Designation | TPI | Class | Max | Min | Max | Min | Max | Min | Class | Min | Max | Min | Max | Min | Max | Basic |  | Basic
7.723 |  | G7.723x0.907 | G 1/16 | 28 | A | 7.723 | 7.509 | 7.142 | 7.035 | 6.561 |  |  | 6.561 | 6.834 | 7.142 | 7.249 | 7.723 |  | 1.5875 | 15.446 | 4.5000
7.723 |  | G7.723x0.907 | G 1/16 | 28 | B | 7.723 | 7.509 | 7.142 | 6.928 | 6.561
9.728 |  | G9.728x0.907 | G 1/8 | 28 | A | 9.728 | 9.514 | 9.147 | 9.040 | 8.566 |  |  | 8.566 | 8.848 | 9.147 | 9.254 | 9.728 |  | 3.1750 | 19.456 | 4.5000
9.728 |  | G9.728x0.907 | G 1/8 | 28 | B | 9.728 | 9.514 | 9.147 | 8.933 | 8.566
13.157 |  | G13.157x1.337 | G 1/4 | 19 | A | 13.157 | 12.907 | 12.301 | 12.176 | 11.445 |  |  | 11.445 | 11.89 | 12.301 | 12.426 | 13.157 |  | 6.3500 | 26.314 | 6.5000
13.157 |  | G13.157x1.337 | G 1/4 | 19 | B | 13.157 | 12.907 | 12.301 | 12.051 | 11.445
16.662 |  | G16.662x1.337 | G 3/8 | 19 | A | 16.662 | 16.412 | 15.806 | 15.681 | 14.950 |  |  | 14.95 | 15.395 | 15.806 | 15.931 | 16.662 |  | 9.5250 | 33.324 | 6.5000
16.662 |  | G16.662x1.337 | G 3/8 | 19 | B | 16.662 | 16.412 | 15.806 | 15.556 | 14.950
20.955 |  | G20.955x1.814 | G 1/2 | 14 | A | 20.955 | 20.671 | 19.793 | 19.651 | 18.631 |  |  | 18.631 | 19.172 | 19.793 | 19.935 | 20.955 |  | 12.7000 | 41.910 | 8.5000
20.955 |  | G20.955x1.814 | G 1/2 | 14 | B | 20.955 | 20.671 | 19.793 | 19.509 | 18.631
22.911 |  | G22.911x1.814 | G 5/8 | 14 | A | 22.911 | 22.627 | 21.749 | 21.607 | 20.587 |  |  | 20.587 | 21.128 | 21.749 | 21.891 | 22.911 |  |  | 45.822 | 8.5000
22.911 |  | G22.911x1.814 | G 5/8 | 14 | B | 22.911 | 22.627 | 21.749 | 21.465 | 20.587
26.441 |  | G26.441x1.814 | G 3/4 | 14 | A | 26.441 | 26.157 | 25.279 | 25.137 | 24.117 |  |  | 24.117 | 24.658 | 25.279 | 25.421 | 26.441 |  | 15.8750 | 52.882 | 8.5000
26.441 |  | G26.441x1.814 | G 3/4 | 14 | B | 26.441 | 26.157 | 25.279 | 24.995 | 24.117
30.201 |  | G30.201x1.814 | G 7/8 | 14 | A | 30.201 | 29.917 | 29.039 | 28.897 | 27.877 |  |  | 27.877 | 28.418 | 29.039 | 29.181 | 30.201 |  | 22.2250 | 60.402 | 8.8000
30.201 |  | G30.201x1.814 | G 7/8 | 14 | B | 30.201 | 29.917 | 29.039 | 28.755 | 27.877
33.249 |  | G33.249x2.309 | G 1 | 11 | A | 33.249 | 32.889 | 31.770 | 31.590 | 30.291 |  |  | 30.291 | 30.931 | 31.77 | 31.95 | 33.249 |  | 25.4000 | 66.498 | 10.0000
33.249 |  | G33.249x2.309 | G 1 | 11 | B | 33.249 | 32.889 | 31.770 | 31.410 | 30.291
37.897 |  | G37.897x2.309 | G 1 1/8 | 11 | A | 37.897 | 37.537 | 36.418 | 36.238 | 34.939 |  |  | 34.939 | 35.579 | 36.418 | 36.598 | 37.897 |  | 28.5750 | 75.794 | 10.0000
37.897 |  | G37.897x2.309 | G 1 1/8 | 11 | B | 37.897 | 37.537 | 36.418 | 36.058 | 34.939
41.910 |  | G41.91x2.309 | G 1 1/4 | 11 | A | 41.910 | 41.550 | 40.431 | 40.251 | 38.952 |  |  | 38.952 | 39.592 | 40.431 | 40.611 | 41.910 |  | 31.7500 | 83.820 | 10.0000
41.910 |  | G41.91x2.309 | G 1 1/4 | 11 | B | 41.910 | 41.550 | 40.431 | 40.071 | 38.952
47.803 |  | G47.803x2.309 | G 1 1/2 | 11 | A | 47.803 | 47.443 | 46.324 | 46.144 | 44.845 |  |  | 44.845 | 45.485 | 46.324 | 46.504 | 47.803 |  | 38.1000 | 95.606 | 10.0000
47.803 |  | G47.803x2.309 | G 1 1/2 | 11 | B | 47.803 | 47.443 | 46.324 | 45.964 | 44.845
53.746 |  | G53.746x2.309 | G 1 3/4 | 11 | A | 53.746 | 53.386 | 52.267 | 52.087 | 50.788 |  |  | 50.788 | 51.428 | 52.267 | 52.447 | 53.746 |  | 44.4500 | 107.492 | 10.0000
53.746 |  | G53.746x2.309 | G 1 3/4 | 11 | B | 53.746 | 53.386 | 52.267 | 51.907 | 50.788
59.614 |  | G59.614x2.309 | G 2 | 11 | A | 59.614 | 59.254 | 58.135 | 57.955 | 56.656 |  |  | 56.656 | 57.296 | 58.135 | 58.315 | 59.614 |  | 50.8000 | 119.228 | 10.0000
59.614 |  | G59.614x2.309 | G 2 | 11 | B | 59.614 | 59.254 | 58.135 | 57.775 | 56.656
65.710 |  | G65.71x2.309 | G 2 1/4 | 11 | A | 65.710 | 65.276 | 64.231 | 64.014 | 62.752 |  |  | 62.752 | 63.392 | 64.231 | 64.448 | 65.710 |  | 57.1500 | 131.420 | 10.0000
65.710 |  | G65.71x2.309 | G 2 1/4 | 11 | B | 65.710 | 65.276 | 64.231 | 63.797 | 62.752
75.184 |  | G75.184x2.309 | G 2 1/2 | 11 | A | 75.184 | 74.750 | 73.705 | 73.488 | 72.226 |  |  | 72.226 | 72.866 | 73.705 | 73.922 | 75.184 |  |  | 150.368 | 10.0000
75.184 |  | G75.184x2.309 | G 2 1/2 | 11 | B | 75.184 | 74.750 | 73.705 | 73.271 | 72.226
81.534 |  | G81.534x2.309 | G 2 3/4 | 11 | A | 81.534 | 81.100 | 80.055 | 79.838 | 78.576 |  |  | 78.576 | 79.216 | 80.055 | 80.272 | 81.534 |  | 69.8500 | 163.068 | 10.0000
81.534 |  | G81.534x2.309 | G 2 3/4 | 11 | B | 81.534 | 81.100 | 80.055 | 79.621 | 78.576
87.884 |  | G87.884x2.309 | G 3 | 11 | A | 87.884 | 87.450 | 86.405 | 86.188 | 84.926 |  |  | 84.926 | 85.566 | 86.405 | 86.622 | 87.884 |  | 76.2000 | 175.768 | 10.0000
87.884 |  | G87.884x2.309 | G 3 | 11 | B | 87.884 | 87.450 | 86.405 | 85.971 | 84.926
100.330 |  | G100.33x2.309 | G 3 1/2 | 11 | A | 100.330 | 99.896 | 98.851 | 98.634 | 97.372 |  |  | 97.372 | 98.012 | 98.851 | 99.068 | 100.330 |  | 88.9000 | 200.660 | 10.0000
100.330 |  | G100.33x2.309 | G 3 1/2 | 11 | B | 100.330 | 99.896 | 98.851 | 98.417 | 97.372
113.030 |  | G113.03x2.309 | G 4 | 11 | A | 113.030 | 112.596 | 111.551 | 111.334 | 110.072 |  |  | 110.072 | 110.712 | 111.551 | 111.768 | 113.030 |  | 101.6000 | 226.060 | 10.0000
113.030 |  | G113.03x2.309 | G 4 | 11 | B | 113.030 | 112.596 | 111.551 | 111.117 | 110.072
125.730 |  | G125.73x2.309 | G 4 1/2 | 11 | A | 125.730 | 125.296 | 124.251 | 124.034 | 122.772 |  |  | 122.772 | 123.412 | 124.251 | 124.468 | 125.730 |  | 114.3000 | 251.460 | 10.0000
125.730 |  | G125.73x2.309 | G 4 1/2 | 11 | B | 125.730 | 125.296 | 124.251 | 123.817 | 122.772
138.430 |  | G138.43x2.309 | G 5 | 11 | A | 138.430 | 137.996 | 136.951 | 136.734 | 135.472 |  |  | 135.472 | 136.112 | 136.951 | 137.168 | 138.430 |  | 127.0000 | 276.860 | 10.0000
138.430 |  | G138.43x2.309 | G 5 | 11 | B | 138.430 | 137.996 | 136.951 | 136.517 | 135.472
151.130 |  | G151.13x2.309 | G 5 1/2 | 11 | A | 151.130 | 150.696 | 149.651 | 149.434 | 148.172 |  |  | 148.172 | 148.812 | 149.651 | 149.868 | 151.130 |  | 139.7000 | 302.260 | 10.0000
151.130 |  | G151.13x2.309 | G 5 1/2 | 11 | B | 151.130 | 150.696 | 149.651 | 149.217 | 148.172
163.830 |  | G163.83x2.309 | G 6 | 11 | A | 163.830 | 163.396 | 162.351 | 162.134 | 160.872 |  |  | 160.872 | 161.512 | 162.351 | 162.568 | 163.830 |  | 152.4000 | 327.660 | 10.0000
163.830 |  | G163.83x2.309 | G 6 | 11 | B | 163.830 | 163.396 | 162.351 | 161.917 | 160.872

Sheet: DIN Pipe Threads
M Q | DIN Pipe Threads |  | Sort Order - 18 |  | External |  |  |  |  |  |  | Internal
 |  |  |  |  |  | Major Dia |  | Pitch Dia |  | Minor Dia |  |  | Minor Dia |  | Pitch Dia |  | Major Dia |  | Tap Drill | Thread Depth | Thread Runouts
Size | Size Suffix | Thread Designation | Custom Thread Designation | TPI | Class | Max | Min | Max | Min | Max | Min | Class | Min | Max | Min | Max | Min | Max | Basic
7.723 |  | G7.723x0.907 | G 1/16 | 28 | A | 7.723 | 7.509 | 7.142 | 7.035 | 6.561 |  |  | 6.561 | 6.834 | 7.142 | 7.249 | 7.723 |  | 1.5875 | 15.446 | 4.5000
7.723 |  | G7.723x0.907 | G 1/16 | 28 | B | 7.723 | 7.509 | 7.142 | 6.928 | 6.561
9.728 |  | G9.728x0.907 | G 1/8 | 28 | A | 9.728 | 9.514 | 9.147 | 9.040 | 8.566 |  |  | 8.566 | 8.848 | 9.147 | 9.254 | 9.728 |  | 3.1750 | 19.456 | 4.5000
9.728 |  | G9.728x0.907 | G 1/8 | 28 | B | 9.728 | 9.514 | 9.147 | 8.933 | 8.566
13.157 |  | G13.157x1.337 | G 1/4 | 19 | A | 13.157 | 12.907 | 12.301 | 12.176 | 11.445 |  |  | 11.445 | 11.89 | 12.301 | 12.426 | 13.157 |  | 6.3500 | 26.314 | 6.5000
13.157 |  | G13.157x1.337 | G 1/4 | 19 | B | 13.157 | 12.907 | 12.301 | 12.051 | 11.445
16.662 |  | G16.662x1.337 | G 3/8 | 19 | A | 16.662 | 16.412 | 15.806 | 15.681 | 14.950 |  |  | 14.95 | 15.395 | 15.806 | 15.931 | 16.662 |  | 9.5250 | 33.324 | 6.5000
16.662 |  | G16.662x1.337 | G 3/8 | 19 | B | 16.662 | 16.412 | 15.806 | 15.556 | 14.950
20.955 |  | G20.955x1.814 | G 1/2 | 14 | A | 20.955 | 20.671 | 19.793 | 19.651 | 18.631 |  |  | 18.631 | 19.172 | 19.793 | 19.935 | 20.955 |  | 12.7000 | 41.910 | 8.5000
20.955 |  | G20.955x1.814 | G 1/2 | 14 | B | 20.955 | 20.671 | 19.793 | 19.509 | 18.631
22.911 |  | G22.911x1.814 | G 5/8 | 14 | A | 22.911 | 22.627 | 21.749 | 21.607 | 20.587 |  |  | 20.587 | 21.128 | 21.749 | 21.891 | 22.911 |  |  | 45.822 | 8.5000
22.911 |  | G22.911x1.814 | G 5/8 | 14 | B | 22.911 | 22.627 | 21.749 | 21.465 | 20.587
26.441 |  | G26.441x1.814 | G 3/4 | 14 | A | 26.441 | 26.157 | 25.279 | 25.137 | 24.117 |  |  | 24.117 | 24.658 | 25.279 | 25.421 | 26.441 |  | 15.8750 | 52.882 | 8.5000
26.441 |  | G26.441x1.814 | G 3/4 | 14 | B | 26.441 | 26.157 | 25.279 | 24.995 | 24.117
30.201 |  | G30.201x1.814 | G 7/8 | 14 | A | 30.201 | 29.917 | 29.039 | 28.897 | 27.877 |  |  | 27.877 | 28.418 | 29.039 | 29.181 | 30.201 |  | 22.2250 | 60.402 | 8.5000
30.201 |  | G30.201x1.814 | G 7/8 | 14 | B | 30.201 | 29.917 | 29.039 | 28.755 | 27.877
33.249 |  | G33.249x2.309 | G 1 | 11 | A | 33.249 | 32.889 | 31.770 | 31.590 | 30.291 |  |  | 30.291 | 30.931 | 31.77 | 31.95 | 33.249 |  | 25.4000 | 66.498 | 10.5000
33.249 |  | G33.249x2.309 | G 1 | 11 | B | 33.249 | 32.889 | 31.770 | 31.410 | 30.291
37.897 |  | G37.897x2.309 | G 1 1/8 | 11 | A | 37.897 | 37.537 | 36.418 | 36.238 | 34.939 |  |  | 34.939 | 35.579 | 36.418 | 36.598 | 37.897 |  | 28.5750 | 75.794 | 10.5000
37.897 |  | G37.897x2.309 | G 1 1/8 | 11 | B | 37.897 | 37.537 | 36.418 | 36.058 | 34.939
41.910 |  | G41.91x2.309 | G 1 1/4 | 11 | A | 41.910 | 41.550 | 40.431 | 40.251 | 38.952 |  |  | 38.952 | 39.592 | 40.431 | 40.611 | 41.910 |  | 31.7500 | 83.820 | 10.5000
41.910 |  | G41.91x2.309 | G 1 1/4 | 11 | B | 41.910 | 41.550 | 40.431 | 40.071 | 38.952
47.803 |  | G47.803x2.309 | G 1 1/2 | 11 | A | 47.803 | 47.443 | 46.324 | 46.144 | 44.845 |  |  | 44.845 | 45.485 | 46.324 | 46.504 | 47.803 |  | 38.1000 | 95.606 | 10.5000
47.803 |  | G47.803x2.309 | G 1 1/2 | 11 | B | 47.803 | 47.443 | 46.324 | 45.964 | 44.845
53.746 |  | G53.746x2.309 | G 1 3/4 | 11 | A | 53.746 | 53.386 | 52.267 | 52.087 | 50.788 |  |  | 50.788 | 51.428 | 52.267 | 52.447 | 53.746 |  | 44.4500 | 107.492 | 10.5000
53.746 |  | G53.746x2.309 | G 1 3/4 | 11 | B | 53.746 | 53.386 | 52.267 | 51.907 | 50.788
59.614 |  | G59.614x2.309 | G 2 | 11 | A | 59.614 | 59.254 | 58.135 | 57.955 | 56.656 |  |  | 56.656 | 57.296 | 58.135 | 58.315 | 59.614 |  | 50.8000 | 119.228 | 10.5000
59.614 |  | G59.614x2.309 | G 2 | 11 | B | 59.614 | 59.254 | 58.135 | 57.775 | 56.656
65.710 |  | G65.71x2.309 | G 2 1/4 | 11 | A | 65.710 | 65.276 | 64.231 | 64.014 | 62.752 |  |  | 62.752 | 63.392 | 64.231 | 64.448 | 65.710 |  | 57.1500 | 131.420 | 10.5000
65.710 |  | G65.71x2.309 | G 2 1/4 | 11 | B | 65.710 | 65.276 | 64.231 | 63.797 | 62.752
75.184 |  | G75.184x2.309 | G 2 1/2 | 11 | A | 75.184 | 74.750 | 73.705 | 73.488 | 72.226 |  |  | 72.226 | 72.866 | 73.705 | 73.922 | 75.184 |  |  | 150.368 | 10.5000
75.184 |  | G75.184x2.309 | G 2 1/2 | 11 | B | 75.184 | 74.750 | 73.705 | 73.271 | 72.226
81.534 |  | G81.534x2.309 | G 2 3/4 | 11 | A | 81.534 | 81.100 | 80.055 | 79.838 | 78.576 |  |  | 78.576 | 79.216 | 80.055 | 80.272 | 81.534 |  | 69.8500 | 163.068 | 10.5000
81.534 |  | G81.534x2.309 | G 2 3/4 | 11 | B | 81.534 | 81.100 | 80.055 | 79.621 | 78.576
87.884 |  | G87.884x2.309 | G 3 | 11 | A | 87.884 | 87.450 | 86.405 | 86.188 | 84.926 |  |  | 84.926 | 85.566 | 86.405 | 86.622 | 87.884 |  | 76.2000 | 175.768 | 10.5000
87.884 |  | G87.884x2.309 | G 3 | 11 | B | 87.884 | 87.450 | 86.405 | 85.971 | 84.926
100.330 |  | G100.33x2.309 | G 3 1/2 | 11 | A | 100.330 | 99.896 | 98.851 | 98.634 | 97.372 |  |  | 97.372 | 98.012 | 98.851 | 99.068 | 100.330 |  | 88.9000 | 200.660 | 10.5000
100.330 |  | G100.33x2.309 | G 3 1/2 | 11 | B | 100.330 | 99.896 | 98.851 | 98.417 | 97.372
113.030 |  | G113.03x2.309 | G 4 | 11 | A | 113.030 | 112.596 | 111.551 | 111.334 | 110.072 |  |  | 110.072 | 110.712 | 111.551 | 111.768 | 113.030 |  | 101.6000 | 226.060 | 10.5000
113.030 |  | G113.03x2.309 | G 4 | 11 | B | 113.030 | 112.596 | 111.551 | 111.117 | 110.072
125.730 |  | G125.73x2.309 | G 4 1/2 | 11 | A | 125.730 | 125.296 | 124.251 | 124.034 | 122.772 |  |  | 122.772 | 123.412 | 124.251 | 124.468 | 125.730 |  | 114.3000 | 251.460 | 10.5000
125.730 |  | G125.73x2.309 | G 4 1/2 | 11 | B | 125.730 | 125.296 | 124.251 | 123.817 | 122.772
138.430 |  | G138.43x2.309 | G 5 | 11 | A | 138.430 | 137.996 | 136.951 | 136.734 | 135.472 |  |  | 135.472 | 136.112 | 136.951 | 137.168 | 138.430 |  | 127.0000 | 276.860 | 10.5000
138.430 |  | G138.43x2.309 | G 5 | 11 | B | 138.430 | 137.996 | 136.951 | 136.517 | 135.472
151.130 |  | G151.13x2.309 | G 5 1/2 | 11 | A | 151.130 | 150.696 | 149.651 | 149.434 | 148.172 |  |  | 148.172 | 148.812 | 149.651 | 149.868 | 151.130 |  | 139.7000 | 302.260 | 10.5000
151.130 |  | G151.13x2.309 | G 5 1/2 | 11 | B | 151.130 | 150.696 | 149.651 | 149.217 | 148.172
163.830 |  | G163.83x2.309 | G 6 | 11 | A | 163.830 | 163.396 | 162.351 | 162.134 | 160.872 |  |  | 160.872 | 161.512 | 162.351 | 162.568 | 163.830 |  | 152.4000 | 327.660 | 10.5000
163.830 |  | G163.83x2.309 | G 6 | 11 | B | 163.830 | 163.396 | 162.351 | 161.917 | 160.872

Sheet: BSP Pipe Threads
M Q | BSP Pipe Threads |  | Sort Order - 19 |  | External |  |  |  |  |  |  | Internal
 |  |  |  |  |  | Major Dia |  | Pitch Dia |  | Minor Dia |  |  | Minor Dia |  | Pitch Dia |  | Major Dia |  | Tap Drill | Thread Depth | Thread Runouts
Size | Size Suffix | Thread Designation | Custom Thread Designation | TPI | Class | Max | Min | Max | Min | Max | Min | Class | Min | Max | Min | Max | Min | Max | Basic |  | Basic
1/16 |  | G 1/16-28 | G 1/16-28 | 28 | A | 7.723 | 7.509 | 7.142 | 7.035 | 6.561 |  |  | 6.561 | 6.834 | 7.142 | 7.249 | 7.723 |  | 6.6000 | 15.4460 | 4.5000
1/16 |  | G 1/16-28 | G 1/16-28 | 28 | B | 7.723 | 7.509 | 7.142 | 7.035 | 6.561
1/8 |  | G 1/8-28 | G 1/8-28 | 28 | A | 9.728 | 9.514 | 9.147 | 9.040 | 8.566 |  |  | 8.566 | 8.848 | 9.147 | 9.254 | 9.728 |  | 8.7300 | 19.4560 | 4.5000
1/8 |  | G 1/8-28 | G 1/8-28 | 28 | B | 9.728 | 9.514 | 9.147 | 9.040 | 8.566
1/4 |  | G 1/4-19 | G 1/4-19 | 19 | A | 13.157 | 12.907 | 12.301 | 12.176 | 11.445 |  |  | 11.445 | 11.89 | 12.301 | 12.426 | 13.157 |  | 11.8000 | 26.3140 | 6.5000
1/4 |  | G 1/4-19 | G 1/4-19 | 19 | B | 13.157 | 12.907 | 12.301 | 12.176 | 11.445
3/8 |  | G 3/8-19 | G 3/8-19 | 19 | A | 16.662 | 16.412 | 15.806 | 15.681 | 14.950 |  |  | 14.95 | 15.395 | 15.806 | 15.931 | 16.662 |  | 15.2500 | 33.3240 | 6.5000
3/8 |  | G 3/8-19 | G 3/8-19 | 19 | B | 16.662 | 16.412 | 15.806 | 15.681 | 14.950
1/2 |  | G 1/2-14 | G 1/2-14 | 14 | A | 20.955 | 20.671 | 19.793 | 19.651 | 18.631 |  |  | 18.631 | 19.172 | 19.793 | 19.935 | 20.955 |  | 19.0500 | 41.9100 | 8.5000
1/2 |  | G 1/2-14 | G 1/2-14 | 14 | B | 20.955 | 20.671 | 19.793 | 19.651 | 18.631
5/8 |  | G 5/8-14 | G 5/8-14 | 14 | A | 22.911 | 22.627 | 21.749 | 21.607 | 20.587 |  |  | 20.587 | 21.128 | 21.749 | 21.891 | 22.911 |  | 21.0000 | 45.8220 | 8.5000
5/8 |  | G 5/8-14 | G 5/8-14 | 14 | B | 22.911 | 22.627 | 21.749 | 21.607 | 20.587
3/4 |  | G 3/4-14 | G 3/4-14 | 14 | A | 26.441 | 26.157 | 25.279 | 25.137 | 24.117 |  |  | 24.117 | 24.658 | 25.279 | 25.421 | 26.441 |  | 24.5000 | 52.8820 | 8.5000
3/4 |  | G 3/4-14 | G 3/4-14 | 14 | B | 26.441 | 26.157 | 25.279 | 25.137 | 24.117
7/8 |  | G 7/8-14 | G 7/8-14 | 14 | A | 30.201 | 29.917 | 29.039 | 28.897 | 27.877 |  |  | 27.877 | 28.418 | 29.039 | 29.181 | 30.201 |  | 28.2500 | 60.4020 | 8.5000
7/8 |  | G 7/8-14 | G 7/8-14 | 14 | B | 30.201 | 29.917 | 29.039 | 28.897 | 27.877
1 |  | G 1-11 | G 1-11 | 11 | A | 33.249 | 32.889 | 31.770 | 31.590 | 30.291 |  |  | 30.291 | 30.931 | 31.77 | 31.95 | 33.249 |  | 30.7500 | 66.4980 | 10.0000
1 |  | G 1-11 | G 1-11 | 11 | B | 33.249 | 32.889 | 31.770 | 31.590 | 30.291
1 1/4 |  | G 1 1/4-11 | G 1 1/4-11 | 11 | A | 41.910 | 41.550 | 40.431 | 40.251 | 38.952 |  |  | 38.952 | 39.592 | 40.431 | 40.611 | 41.910 |  | 39.5000 | 83.8200 | 10.0000
1 1/4 |  | G 1 1/4-11 | G 1 1/4-11 | 11 | B | 41.910 | 41.550 | 40.431 | 40.251 | 38.952
1 1/2 |  | G 1 1/2-11 | G 1 1/2-11 | 11 | A | 47.803 | 47.443 | 46.324 | 46.144 | 44.845 |  |  | 44.845 | 45.485 | 46.324 | 46.504 | 47.803 |  | 45.5000 | 95.6060 | 10.0000
1 1/2 |  | G 1 1/2-11 | G 1 1/2-11 | 11 | B | 47.803 | 47.443 | 46.324 | 46.144 | 44.845
1 3/4 |  | G 1 3/4-11 | G 1 3/4-11 | 11 | A | 53.746 | 53.386 | 52.267 | 52.087 | 50.788 |  |  | 50.788 | 51.428 | 52.267 | 52.447 | 53.746 |  | 51.0000 | 107.4920 | 10.0000
1 3/4 |  | G 1 3/4-11 | G 1 3/4-11 | 11 | B | 53.746 | 53.386 | 52.267 | 52.087 | 50.788
2 |  | G 2-11 | G 2-11 | 11 | A | 59.614 | 59.254 | 58.135 | 57.955 | 56.656 |  |  | 56.656 | 57.296 | 58.135 | 58.315 | 59.614 |  | 57.0000 | 119.2280 | 10.0000
2 |  | G 2-11 | G 2-11 | 11 | B | 59.614 | 59.254 | 58.135 | 57.955 | 56.656
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

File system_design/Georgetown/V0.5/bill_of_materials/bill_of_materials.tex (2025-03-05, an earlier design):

%%%%%%%%%%%%%%%%%%%%%%%%%%%%%%%%%%%%%%%%%%%%%%%%%%%%%%%%%%%%%%%%%%%%%%%%%%%%%
%%%%                NSF requirement, DO NOT ADJUST                             %    
\documentclass[11pt,letterpaper]{article}
\usepackage{mathptmx} % added for time new roman font                        %
\usepackage[left=1in,right=1in,top=1in,bottom=1in]{geometry}                %
%%%%%%%%%%%%%%%%%%%%%%%%%%%%%%%%%%%%%%%%%%%%%%%%%%%%%%%%%%%%%%%%%%%%%%%%%%%%%

\usepackage[latin1]{inputenc}
\usepackage{amsmath}
\usepackage{amsfonts}
\usepackage{amssymb}
\usepackage{graphicx}
\usepackage{paralist}
\usepackage{placeins}        % Added for \FloatBarrier
\usepackage{enumitem}        % Added for changes in \item
\usepackage{commath}         % added for \norm
\usepackage{wrapfig}
\usepackage{tabu}
\usepackage{float}
\usepackage{booktabs}
\usepackage{url}
\usepackage{siunitx}
%\usepackage[sorting=none]{biblatex}
%\bibliography{references}
%\usepackage{arydshln}        % added for \hdashline
\usepackage[table]{xcolor}
\usepackage[colorinlistoftodos,textsize=tiny]{todonotes}
\usepackage[numbers,sort&compress]{natbib}
\bibliographystyle{Downey_NSF}
\usepackage[hidelinks]{hyperref}		% added for custom .bst file, as explained here. https://tex.stackexchange.com/questions/67444/doi-in-ieeetran-bibliography
% Added by Corinne
\usepackage{longtable} 		% added for longer tables
\usepackage{hhline} 		% added for double horizontal lines
\usepackage{subcaption}		% added for side by side tables
\usepackage{arydshln}		% added for dashed hline
\usepackage{multirow}		% added for merging rows in tables
\usepackage{soul}			% added for strike out
%set page header and footer

% packages added by Austin Downey for the maths
\usepackage{amsbsy} % added to use \pmb or poor mans bold
\usepackage{txfonts} % added for \muup and other upright greek letters
\usepackage{upgreek}

% adjust the spacing around section titles
\usepackage{titlesec}
\titlespacing*{\section}
{0pt}{2ex}{0.8ex}
\titlespacing*{\subsection}
{0pt}{1ex}{0.8ex}
\titlespacing*{\subsubsection}
{0pt}{0.8ex}{0.4ex}

\newcommand{\tb}[1]{\textbf{#1}}
\newcommand{\eq}[1]{\begin{equation}{#1}\end{equation}}
\newcommand{\eqs}[1]{\begin{equation}\begin{split}{#1}\end{split}\end{equation}}

\usepackage{color} % color added for editing
\newcommand{\bl}[1]{\textcolor[rgb]{0.00,0.00,1.00}{#1}}
\newcommand{\gr}[1]{\textcolor[rgb]{0.00,0.50,0.00}{#1}}
\newcommand{\rd}[1]{\textcolor[rgb]{0.75,0.00,0.00}{#1}}
\newcommand{\tl}[1]{\textcolor[rgb]{0,0.6,0.60}{#1}}

\newcommand{\thrustsection}[2]{\noindent \textbf{Task #1:}{ \textbf{#2}}}
\newcommand{\tasksection}[2]{\noindent \emph{Task #1:}{ \emph{#2}}}

\DeclareMathAlphabet{\mathpzc}{OT1}{pzc}{m}{it}
\newcommand\myrightarrowline{\mathrel{\ooalign{$\rightarrow$\cr%
			\kern-.15ex\raise.275ex\hbox{\scalebox{1}[0.522]{$\mid$}}\cr}}}

\begin{document}
	
	\begin{center}
		{\Large\textbf{Bill of Materials}}
	\end{center}

\noindent Bill of materials broken down by base package and optional solar and EPM add-on modules. Base package total cost is 117.71 USD.

\setlength{\abovedisplayskip}{3pt}
\setlength{\belowdisplayskip}{3pt}

\begin{longtable}{ p{1.75cm} p{4cm} p{1.25cm} p{1cm} p{1cm} p{2cm} p{2.5cm} }	
	%\centering
	\caption{Base package bill of materials.} 
	\label{components} \\
	%	\todo{can we put the distributors then add the urls in an appendix?}
	\toprule
	Designator & Component & Number of units & Cost per unit [USD] & Total cost [USD] & Source of materials & Material type \\
	\midrule
	Arduino Nano & Arduino Nano & 1 & 24.90 & 24.90 & Arduino & Semiconductor \\
	
	\rowcolor[gray]{0.925}
	Micro SD card module & UMLIFE Micro SD SDHC TF card adaptor reader module with SPI interface & 1 & 0.89 & 0.89 & UMLIFE & Other \\
	
	NRF24L01+ & NRF24L01+ 2.4GHz Wireless RF Transceiver Module & 1 & 1.40 & 1.40 & MakerFocus & Semiconductor \\ 
	
	\rowcolor[gray]{0.925}
	DS3231 real-time clock & DS3231M+ & 1 & 13.31 & 13.31 & Maxim Integrated & Semiconductor \\ 
	
	BME280 environmental sensor & BME280 & 1 & 5.245 & 5.245 & Onyehn & Semiconductor \\ 
	
	\rowcolor[gray]{0.925}
	INA219 current sensor & INA219BIDR & 1 & 2.51 & 2.51 & Texas Instruments & Semiconductor \\ 
	
	N42 permanent magnet & Neodymium Disc Magnet - 1 1/4" Dia x 3/8" Thi & 1 & 12.67 & 12.67 & K\&J Magnetics Inc & Other \\ 
	
	\rowcolor[gray]{0.925}
	Ultrasonic sensor & RCWL-1601 & 1 & 3.95 & 3.95 & Adafruit Industries LLC & Other \\
	
	2s 7.4V LiPo battery & Zeee 2S Lipo Battery 1500mAh 7.4V 60C with Deans Plug & 1 & 13.50 & 13.50 & Zeee & Other \\
	
	\rowcolor[gray]{0.925}
	CR-1025 3V Li+ coin cell & CR-1025-ND & 1 & 1.09 & 1.09 & Jauch Quartz & Other \\
	
	RTC coin cell holder & BK-870 & 1 & 0.58 & 0.58 & MPD & Other \\
	
	\rowcolor[gray]{0.925}
	Main PCB & Main board & 1 & 8.23 & 8.23 & See repository & Other \\
	
	Daughter PCB & Daughter board & 1 & 4.13 & 4.13 & See repository & Other \\
	
	\rowcolor[gray]{0.925}
	Micro SD card & Gigastone 8GB 10-Pack Micro SD Card, Full HD Video 80MB/s Micro SDHC Class 10 & 1 & 3.00 & 3.00 & Gigastone & Other \\

	Slide switch & SS-12D07-VG 4 NS GA PA & 1 & 0.85 & 0.85 & C\&K & Other \\
	
	\rowcolor[gray]{0.925}
	LED & L314ED & 1 & 0.20 & 0.20 & American Opto Plus LED & Semiconductor \\

	PNP transistor & BCP51-16-TP & 1 & 0.48 & 0.48 & Micro Commercial Co & Semiconductor \\
	
	\rowcolor[gray]{0.925}
	NPN Transistor & BCP54 & 1 & 0.77 & 0.77 & onsemi & Semiconductor \\

	Resistors & RES SMD (100, 1k, 4.7k) OHM 1\% 1/4W 1206 & 7 & 0.10 & 0.70 & Digikey & Semiconductor \\
	
	\rowcolor[gray]{0.925}
	Shunt resistor & ERJ-8BSJR10V RES 0.1 OHM 5\% 1/2W 1206 & 1 & 0.40 & 0.40 & Panasonic & Semiconductor \\

	Capacitors & C1206S104K5RACAUTO 0.1 $\mu$F 10\% 50V Ceramic Capacitor X7R 1206 (3216 Metric) & 4 & 0.42 & 1.68 & Kemet & Semiconductor \\
	
	\rowcolor[gray]{0.925}
	5V regulator & MIC5239-5.0YS-TR & 2 & 3.58 & 7.16 & Microchip Technology & Semiconductor \\  

	4" PVC pipe & Schedule 40 Clear Pipe, Non-threaded,  & 1 & 6.54 & 6.54 & Grainger & Polymer \\  

	\rowcolor[gray]{0.925}
	Dean's connector & PRT-11864  & 1 & 1.05 & 1.05 & Sparkfun Electronics & Other \\

	Female HC-SR04 connector & SSA-104-W-T & 1 & 0.91 & 0.91 & Samtec & Other \\ 
	
	\rowcolor[gray]{0.925}
	Female magnet connector & SSA-103-W-G & 1 & 1.29 & 1.29 & Samtec & Other \\ 

	Female daughter board connector & PPPC071LGBN-RC & 1 & 0.67 & 0.67 & Sullins Connector Solutions & Other \\

	\rowcolor[gray]{0.925}
	Male daughter board connector & 0022284070 & 1 & 0.30 & 0.30 & Molex & Other \\ 
	
	\bottomrule
\end{longtable}

\pagebreak

\end{document}

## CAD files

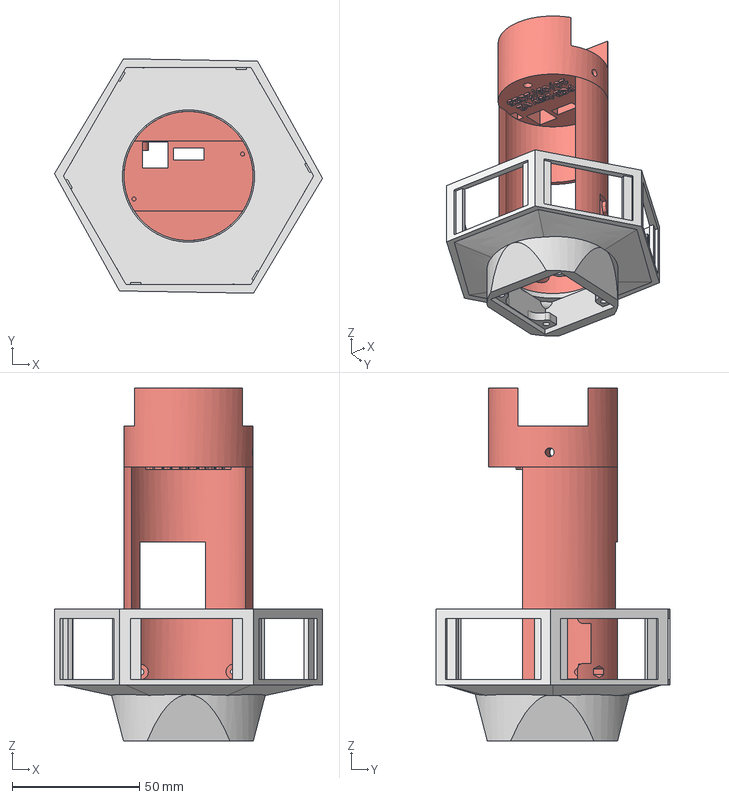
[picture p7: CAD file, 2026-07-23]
system_design/Georgetown/V0.6.0/CAD/6_panel_vertical_chassis/6_panel_vertical_chassis.stp
105.4 x 92.2 x 138.8 mm
PCB tray CAD v2

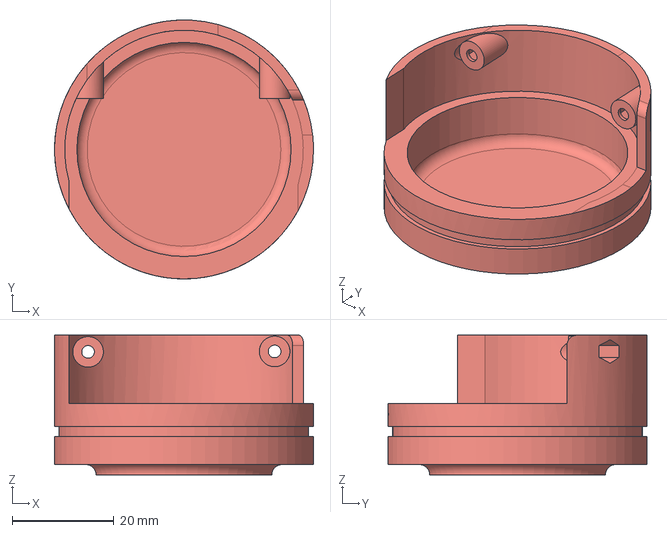
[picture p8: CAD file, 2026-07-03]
system_design/Georgetown/V0.6.0/CAD/CAD 0.5/O-ring groove test/IR 24-5.step
50.8 x 50.8 x 27.4 mm

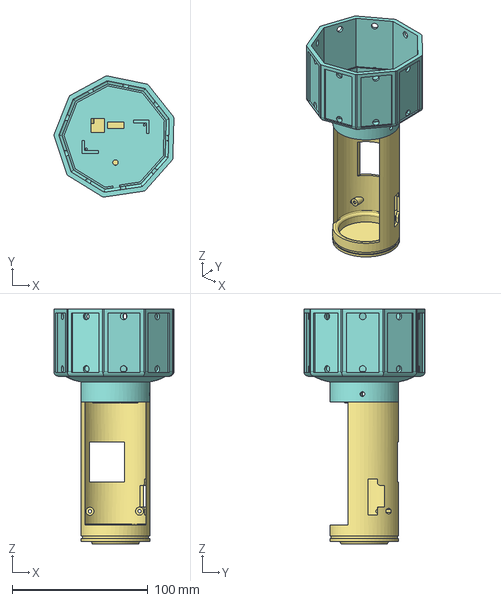
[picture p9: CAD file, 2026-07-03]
system_design/Georgetown/V0.6.0/CAD/CAD 0.5/PCB tray CAD v2.step
88.4 x 89.3 x 173.2 mm

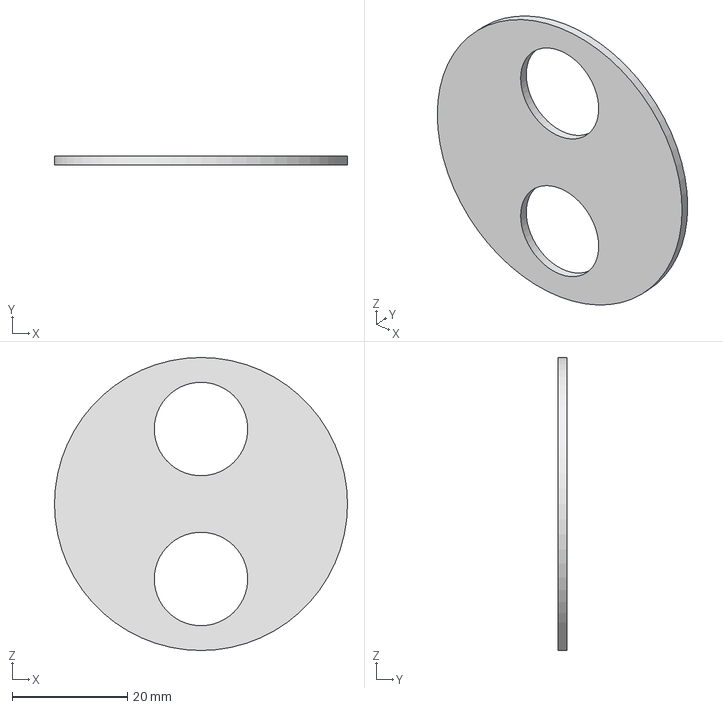
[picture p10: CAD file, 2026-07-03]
system_design/Georgetown/V0.6.0/CAD/Metal base plate/metal_base_plate.stp
50.8 x 1.50 x 50.8 mm

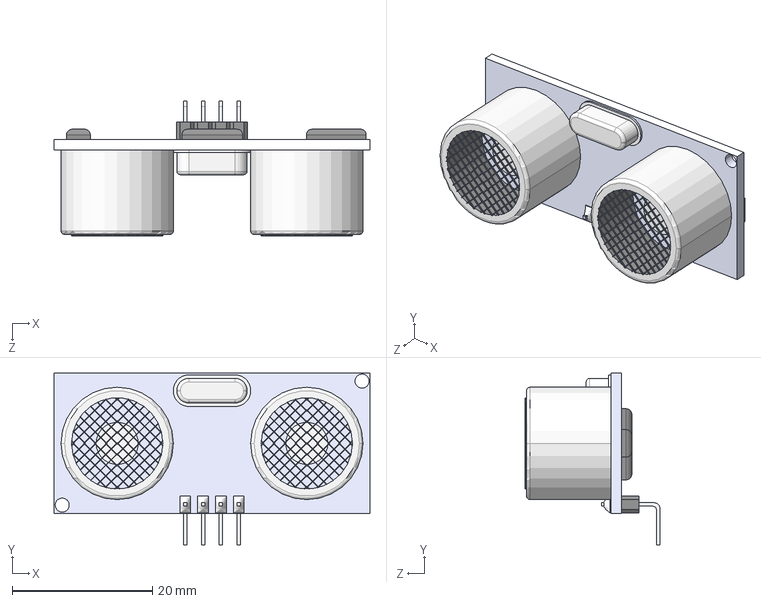
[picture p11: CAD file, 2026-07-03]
system_design/Georgetown/V0.6.0/CAD/Ultrasonic HCSR04.STEP
45.0 x 24.5 x 19.2 mm

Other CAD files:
system_design/Georgetown/V0.6.0/CAD/CAD 0.5/Templates/English/ANSI (in).dwg
system_design/Georgetown/V0.6.0/CAD/CAD 0.5/Templates/Metric/GB.dwg
system_design/Georgetown/V0.6.0/CAD/CAD 0.5/Templates/Standard.dwg
system_design/Georgetown/V0.6.0/CAD/CAD 0.5/O-ring groove test/IR 23-7.step
system_design/Georgetown/V0.6.0/CAD/CAD 0.5/Templates/Metric/JIS.dwg
system_design/Georgetown/V0.6.0/CAD/CAD 0.5/O-ring groove test/IR 23-8.step
system_design/Georgetown/V0.6.0/CAD/CAD 0.5/Templates/Metric/ANSI (mm).dwg
system_design/Georgetown/V0.6.0/CAD/CAD 0.5/O-ring groove test/IR 24-4.step
system_design/Georgetown/V0.6.0/CAD/CAD 0.5/Templates/Metric/GOST.dwg
system_design/Georgetown/V0.6.0/CAD/CAD 0.5/O-ring groove test/IR 24-2.step
system_design/Georgetown/V0.6.0/CAD/CAD 0.5/Templates/Metric/DIN.dwg
system_design/Georgetown/V0.6.0/CAD/CAD 0.5/O-ring groove test/IR 23-6.step
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

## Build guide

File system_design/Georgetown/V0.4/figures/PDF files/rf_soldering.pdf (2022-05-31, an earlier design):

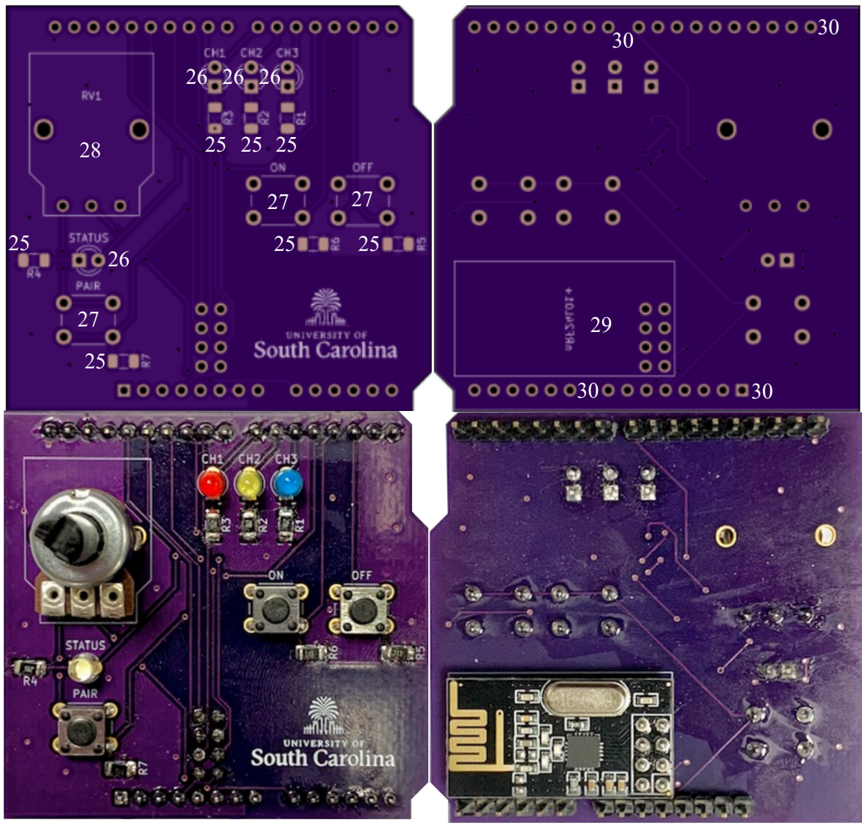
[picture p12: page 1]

25 25 25

25 | 25 | 25
| 26 26 26

28

| 27 | 27

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
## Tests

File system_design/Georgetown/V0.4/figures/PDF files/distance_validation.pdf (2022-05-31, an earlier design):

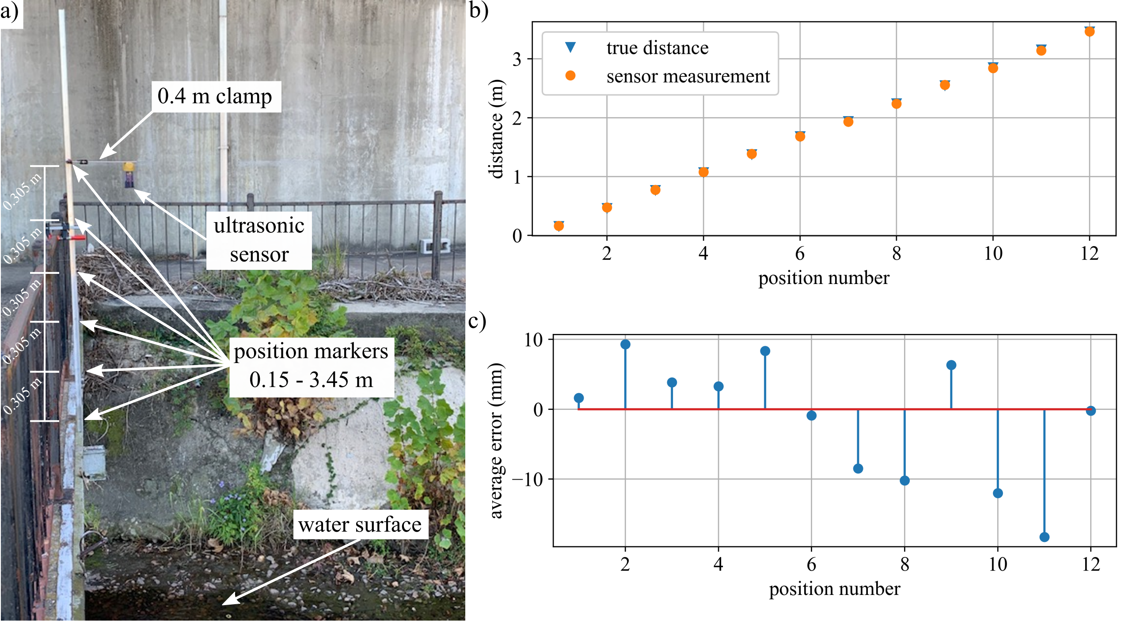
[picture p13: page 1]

ultrasonic
sensor

position markers
0.15 - 3.45 m

water surface

a)

0.4 m clamp

b)

c)

0.305 m

0.305 m

0.305 m

0.305 m

0.305 m

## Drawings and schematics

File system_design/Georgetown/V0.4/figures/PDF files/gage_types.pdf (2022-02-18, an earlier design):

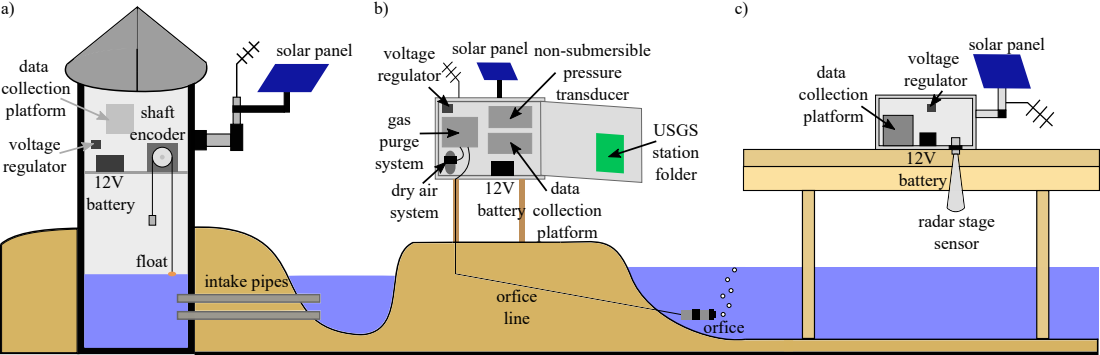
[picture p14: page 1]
solar panel; radar stage sensor; voltage regulator; 12V battery; data collection platform; dry air system; non-submersible pressure transducer; USGS station folder; gas purge system; orfice; float; shaft encoder; intake pipes; orfice line

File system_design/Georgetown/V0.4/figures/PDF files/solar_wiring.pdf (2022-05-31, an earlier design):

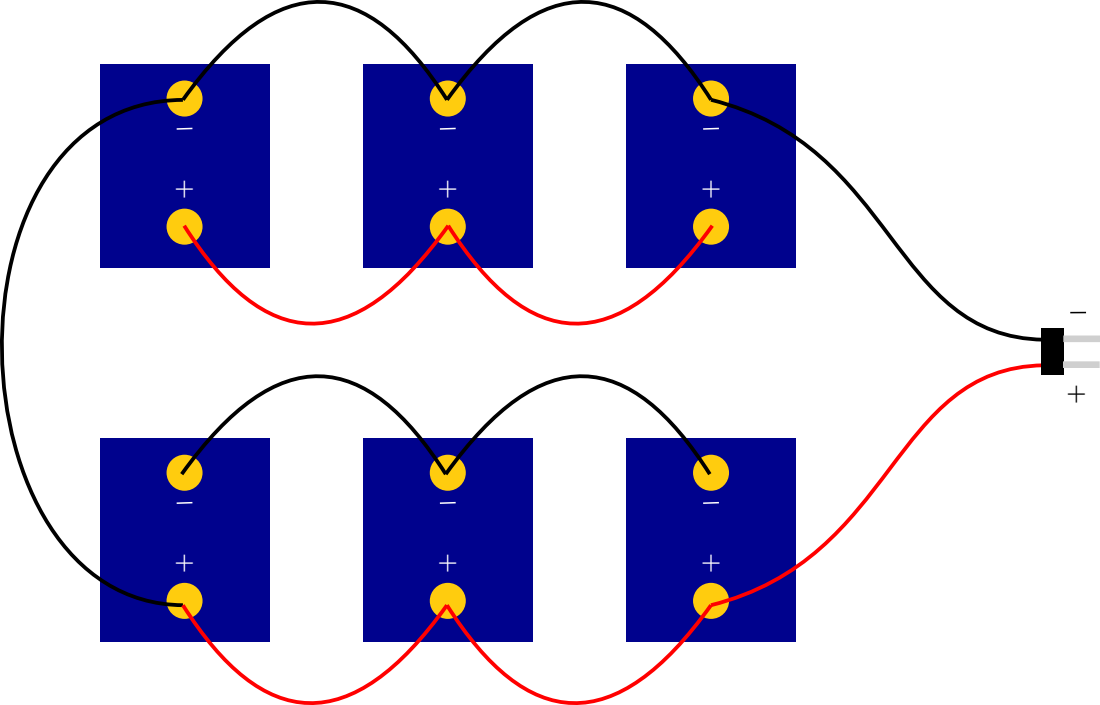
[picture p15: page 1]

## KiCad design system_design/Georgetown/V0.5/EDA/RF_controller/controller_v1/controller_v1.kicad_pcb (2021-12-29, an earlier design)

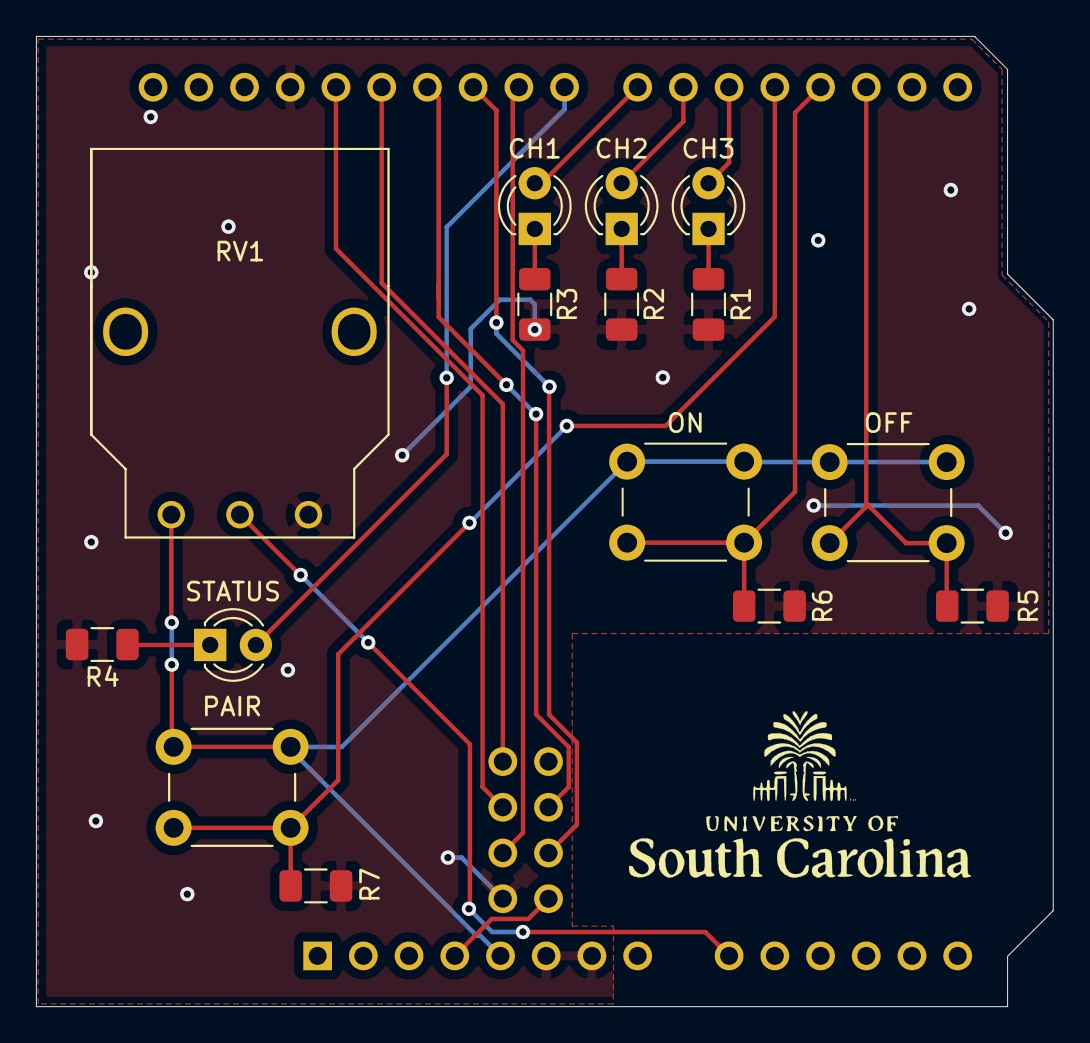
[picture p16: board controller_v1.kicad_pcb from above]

Board: 2 copper layers, 56.5 x 53.9 mm, 17 parts (1 on the bottom side), 20 nets.

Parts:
A1: Arduino_UNO_R3
CH1, CH2, CH3: LED; LED_D3.0mm
OFF: SW_Push; SW_PUSH_6mm
ON: SW_Push; SW_PUSH_6mm
PAIR: SW_Push; SW_PUSH_6mm
R1, R2, R3, R4, R5, R6, R7: R; R_1206_3216Metric
RV1: R_POT; Bourns_PDB12
STATUS: LED; LED_D3.0mm
nRF24L01+: nRF24L01+

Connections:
GND: A1.6, A1.7, A1.29, R1.2, R2.2, R3.2, R4.2, R5.1, R6.2, R7.2, RV1.3, nRF24L01+.5
unnamed: A1.4, nRF24L01+.1
unnamed: A1.5, OFF.1, ON.1, PAIR.1, RV1.1
unnamed: A1.9, RV1.2
unnamed: A1.17, OFF.2, R5.2
unnamed: A1.18, ON.2, R6.1
unnamed: A1.19, PAIR.2, R7.1
unnamed: A1.20, CH3.2
unnamed: A1.21, CH2.2
unnamed: A1.22, CH1.2
unnamed: A1.23, STATUS.2
unnamed: A1.24, nRF24L01+.6
unnamed: A1.25, nRF24L01+.2
unnamed: A1.26, nRF24L01+.3
unnamed: A1.27, nRF24L01+.8
unnamed: A1.28, nRF24L01+.7
unnamed: CH3.1, R1.1
unnamed: CH2.1, R2.1
unnamed: CH1.1, R3.1
unnamed: R4.1, STATUS.1

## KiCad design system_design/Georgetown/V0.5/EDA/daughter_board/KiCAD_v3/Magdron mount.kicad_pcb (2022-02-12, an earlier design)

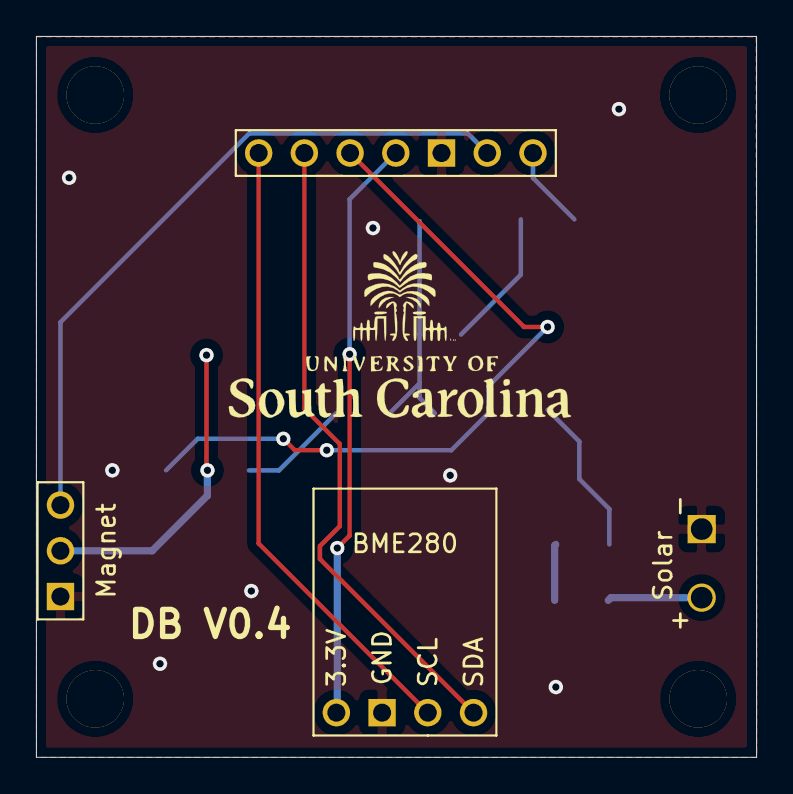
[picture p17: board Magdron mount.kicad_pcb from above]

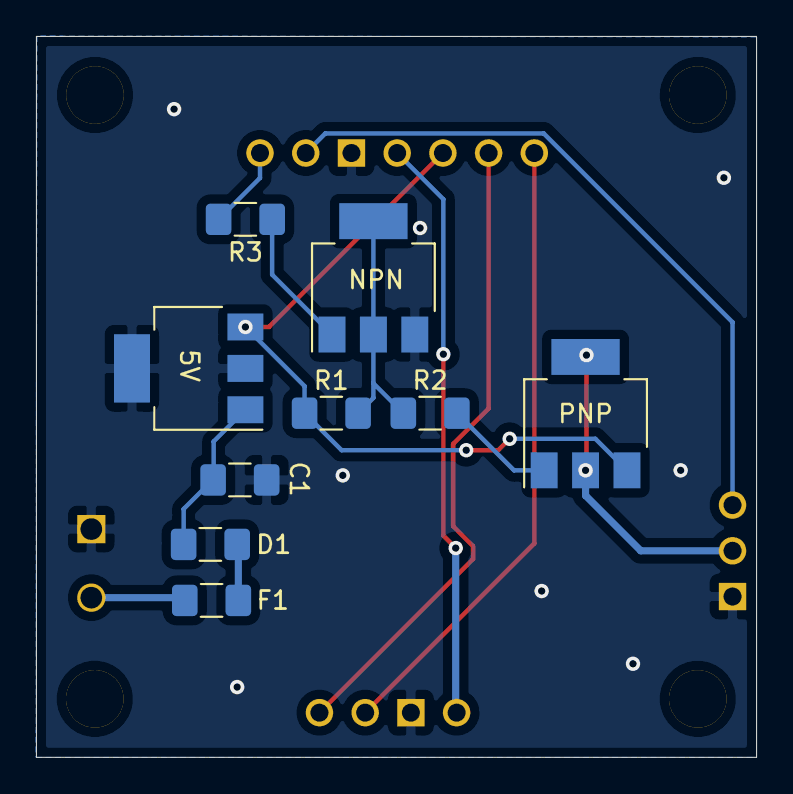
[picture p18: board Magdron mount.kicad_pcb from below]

Board: 2 copper layers, 40.0 x 40.0 mm, 18 parts (10 on the bottom side), 14 nets.

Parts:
5V: KA78M05_TO252; SOT-223-3_TabPin2
.: .; uofsc_logo_0_75in
.#2, .#3, .#4, .#5: MountingHole_3.2mm_M3_DIN965_Pad
BME280: BME280
C1: C; R_1206_3216Metric_Pad1.42x1.75mm_HandSolder
D1: D; R_1206_3216Metric_Pad1.42x1.75mm_HandSolder
F1: Fuse; R_1206_3216Metric_Pad1.42x1.75mm_HandSolder
Magnet: MAG-MAG; Magnet
NPN: BCP56; SOT-223-3_TabPin2
PNP: BCP51; SOT-223-3_TabPin2
R1: 1k; R_1206_3216Metric_Pad1.42x1.75mm_HandSolder
R2, R3: 100; R_1206_3216Metric_Pad1.42x1.75mm_HandSolder
Solar: power_input; XT60PW
U4: top_rail_v2

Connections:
GND: 5V.2, BME280.2, C1.1, Magnet.1, NPN.3, Solar.1, U4.6
unnamed: Magnet.2, PNP.2
unnamed: Magnet.3, U4.7
unnamed: 5V.1, C1.2, D1.1
unnamed: D1.2, F1.1
unnamed: F1.2, Solar.2
unnamed: PNP.1, R2.1
unnamed: 5V.3, PNP.3, R1.1, U4.4
unnamed: NPN.1, R3.1
unnamed: NPN.2, R1.2, R2.2
unnamed: R3.2, U4.8
unnamed: BME280.1, U4.5
unnamed: BME280.3, U4.2
unnamed: BME280.4, U4.3

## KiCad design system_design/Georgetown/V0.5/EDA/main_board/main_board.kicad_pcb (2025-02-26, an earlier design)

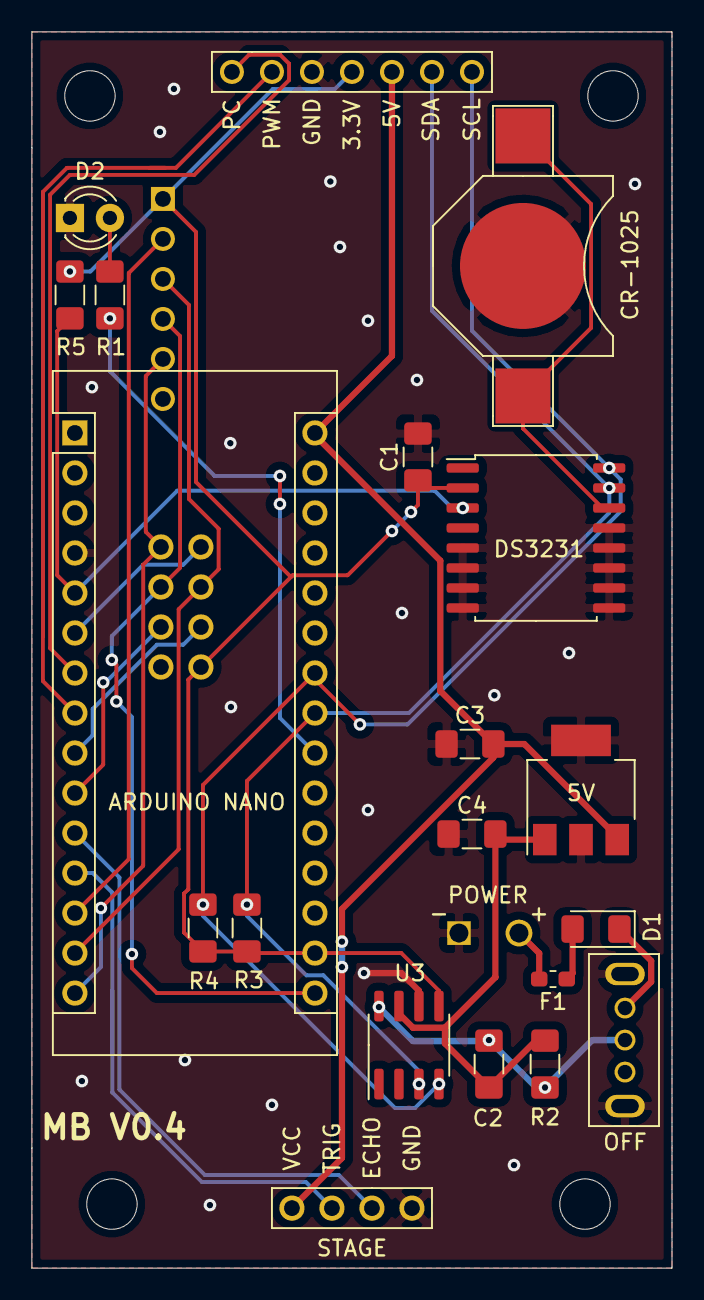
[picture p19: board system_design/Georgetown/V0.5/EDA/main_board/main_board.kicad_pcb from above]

Board: 2 copper layers, 40.6 x 78.5 mm, 23 parts (0 on the bottom side), 25 nets.

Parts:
5V: KA78M05_TO252; SOT-223-3_TabPin2
ARDUINO NANO: Arduino_Nano_v2.x-MCU_Module; Arduino_Nano
C1, C2, C3, C4: C; C_1206_3216Metric_Pad1.42x1.75mm_HandSolder
CR-1025: Battery_Cell; battery_holder_10mm
D1: D; D_1206_3216Metric_Pad1.42x1.75mm_HandSolder
D2: LED; LED_D3.0mm
DS3231: DS3231M; SOIC-16W_7.5x10.3mm_P1.27mm
F1: Fuse; R_0603_1608Metric_Pad1.05x0.95mm_HandSolder
MICRO SD: small_microSD; small_microSD_v2
POWER: XP60PW; XT60PW
R1: 1k; C_1206_3216Metric_Pad1.42x1.75mm_HandSolder
R2: Rs; R_1206_3216Metric_Pad1.42x1.75mm_HandSolder
R3, R4: 4.7k; C_1206_3216Metric_Pad1.42x1.75mm_HandSolder
R5: 4.7k; R_1206_3216Metric_Pad1.42x1.75mm_HandSolder
STAGE: HCSR04
U1: top_rail_v2
U3: INA219AxD; SOIC-8_3.9x4.9mm_P1.27mm
nRF24L01+1: nRF24L01+
switch1: grounded_switch

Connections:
GND: 5V.2, ARDUINO NANO.4, ARDUINO NANO.29, C1.2, C3.1, C4.1, CR-1025.2, D2.1, DS3231.5, DS3231.6, DS3231.7, DS3231.8, DS3231.9, DS3231.10, DS3231.11, DS3231.12, DS3231.13, MICRO SD.6, POWER.1, STAGE.1, U1.6, U3.6, nRF24L01+1.5, switch1.4, switch1.5
unnamed: ARDUINO NANO.5, DS3231.3, R5.1
unnamed: ARDUINO NANO.6, nRF24L01+1.4
unnamed: ARDUINO NANO.7, U1.8
unnamed: ARDUINO NANO.8, U1.7
unnamed: ARDUINO NANO.9, nRF24L01+1.2
unnamed: ARDUINO NANO.10, nRF24L01+1.6
unnamed: ARDUINO NANO.11, STAGE.2
unnamed: ARDUINO NANO.12, STAGE.3
unnamed: ARDUINO NANO.13, MICRO SD.2
unnamed: ARDUINO NANO.14, MICRO SD.3, nRF24L01+1.3
unnamed: ARDUINO NANO.15, MICRO SD.5, nRF24L01+1.8
unnamed: ARDUINO NANO.16, MICRO SD.4, nRF24L01+1.7
unnamed: ARDUINO NANO.17, C1.1, DS3231.2, MICRO SD.1, R3.1, R4.1, R5.2, U1.5, U3.5, nRF24L01+1.1
unnamed: ARDUINO NANO.22, R1.1
unnamed: ARDUINO NANO.23, DS3231.15, R3.2, U1.3, U3.3
unnamed: ARDUINO NANO.24, DS3231.16, R4.2, U1.2, U3.4
unnamed: 5V.3, ARDUINO NANO.30, C3.2, STAGE.4, U1.4
unnamed: CR-1025.1, DS3231.14
unnamed: C2.1, R2.1, U3.8, switch1.2
unnamed: 5V.1, C2.2, C4.2, R2.2, U3.7
unnamed: D1.1, switch1.1
unnamed: D1.2, F1.1
unnamed: D2.2, R1.2
unnamed: F1.2, POWER.2

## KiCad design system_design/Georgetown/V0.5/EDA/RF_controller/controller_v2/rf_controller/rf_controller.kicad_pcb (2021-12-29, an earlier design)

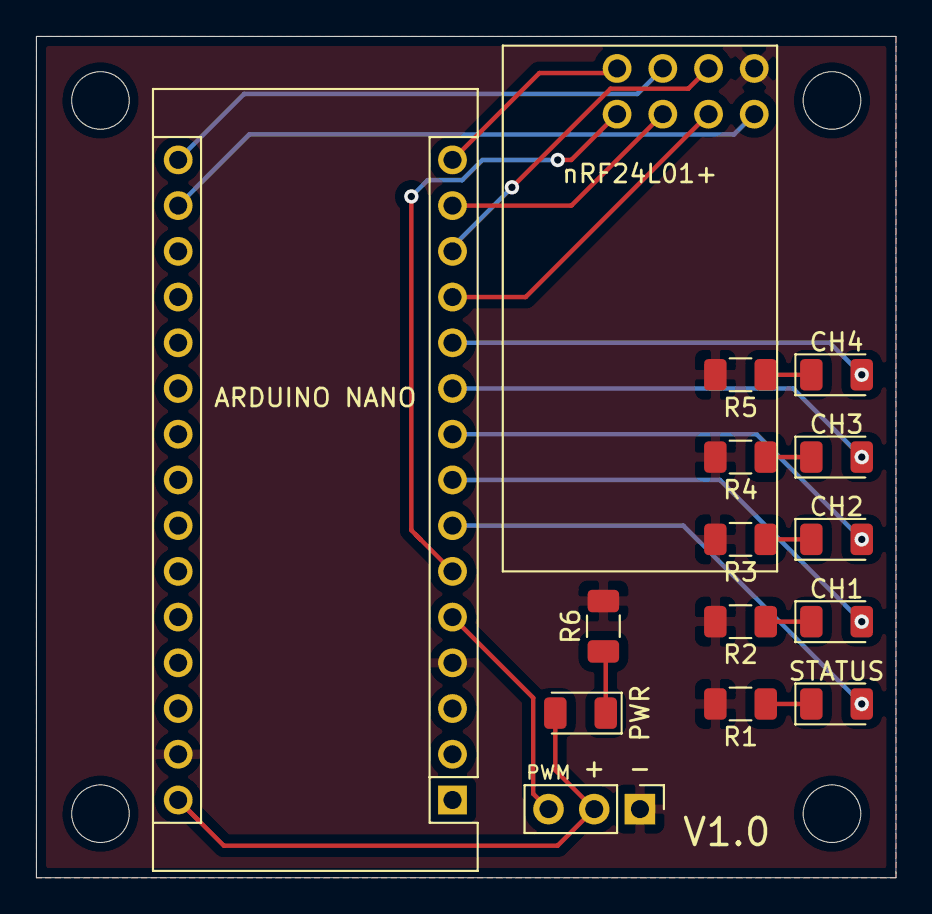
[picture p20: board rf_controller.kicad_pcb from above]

Board: 2 copper layers, 47.8 x 46.7 mm, 15 parts (1 on the bottom side), 21 nets.

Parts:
ARDUINO NANO: Arduino_Nano_v2.x; Arduino_Nano
CH1, CH2, CH3, CH4: LED; LED_1206_3216Metric
PWM: Conn_01x03_Male; PinHeader_1x03_P2.54mm_Vertical
PWR: LED; LED_1206_3216Metric
R1, R2, R3, R4, R5, R6: R; R_1206_3216Metric
STATUS: LED; LED_1206_3216Metric
nRF24L01+: nRF24L01+

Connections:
GND: ARDUINO NANO.4, ARDUINO NANO.29, PWM.1, R1.2, R2.2, R3.2, R4.2, R5.2, R6.2, nRF24L01+.5
unnamed: ARDUINO NANO.5, PWM.3
unnamed: ARDUINO NANO.6, nRF24L01+.4
unnamed: ARDUINO NANO.7, STATUS.2
unnamed: ARDUINO NANO.8, CH1.2
unnamed: ARDUINO NANO.9, CH2.2
unnamed: ARDUINO NANO.10, CH3.2
unnamed: ARDUINO NANO.11, CH4.2
unnamed: ARDUINO NANO.12, nRF24L01+.2
unnamed: ARDUINO NANO.13, nRF24L01+.6
unnamed: ARDUINO NANO.14, nRF24L01+.3
unnamed: ARDUINO NANO.15, nRF24L01+.8
unnamed: ARDUINO NANO.16, nRF24L01+.7
unnamed: ARDUINO NANO.17, nRF24L01+.1
unnamed: ARDUINO NANO.30, PWM.2, PWR.2
unnamed: R1.1, STATUS.1
unnamed: CH1.1, R2.1
unnamed: CH2.1, R3.1
unnamed: CH3.1, R4.1
unnamed: CH4.1, R5.1
unnamed: PWR.1, R6.1

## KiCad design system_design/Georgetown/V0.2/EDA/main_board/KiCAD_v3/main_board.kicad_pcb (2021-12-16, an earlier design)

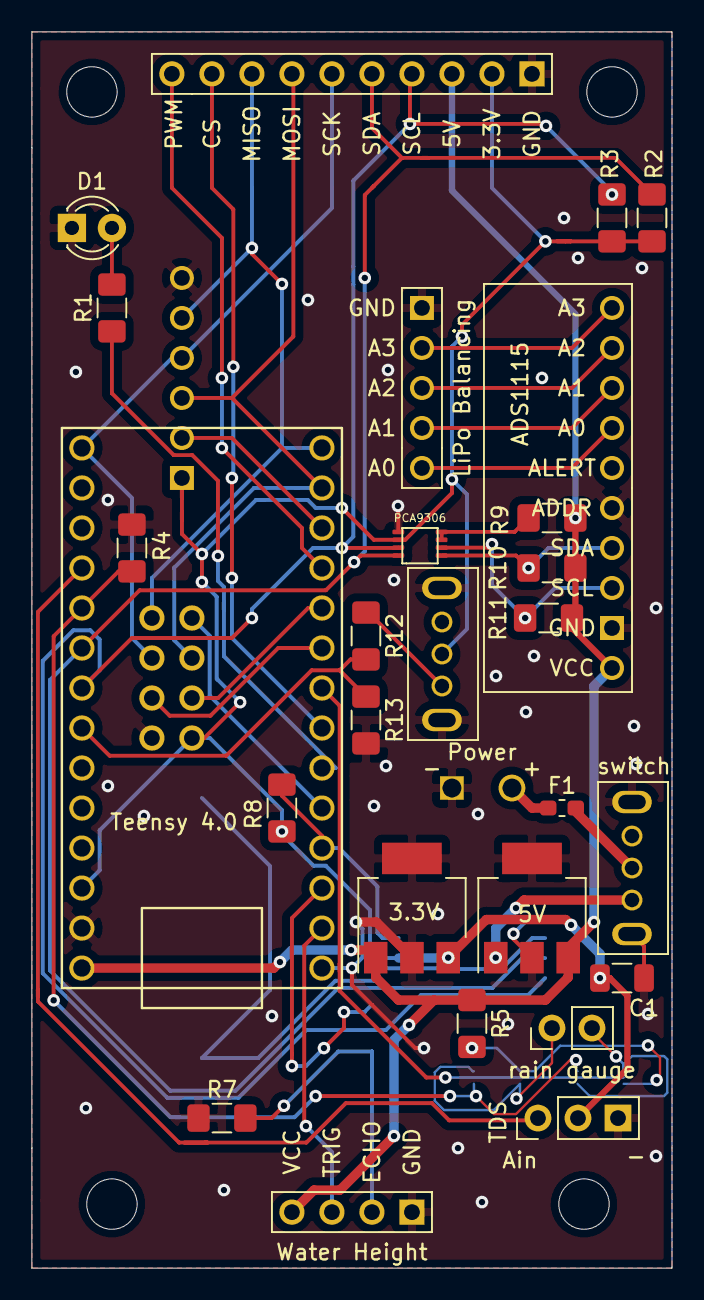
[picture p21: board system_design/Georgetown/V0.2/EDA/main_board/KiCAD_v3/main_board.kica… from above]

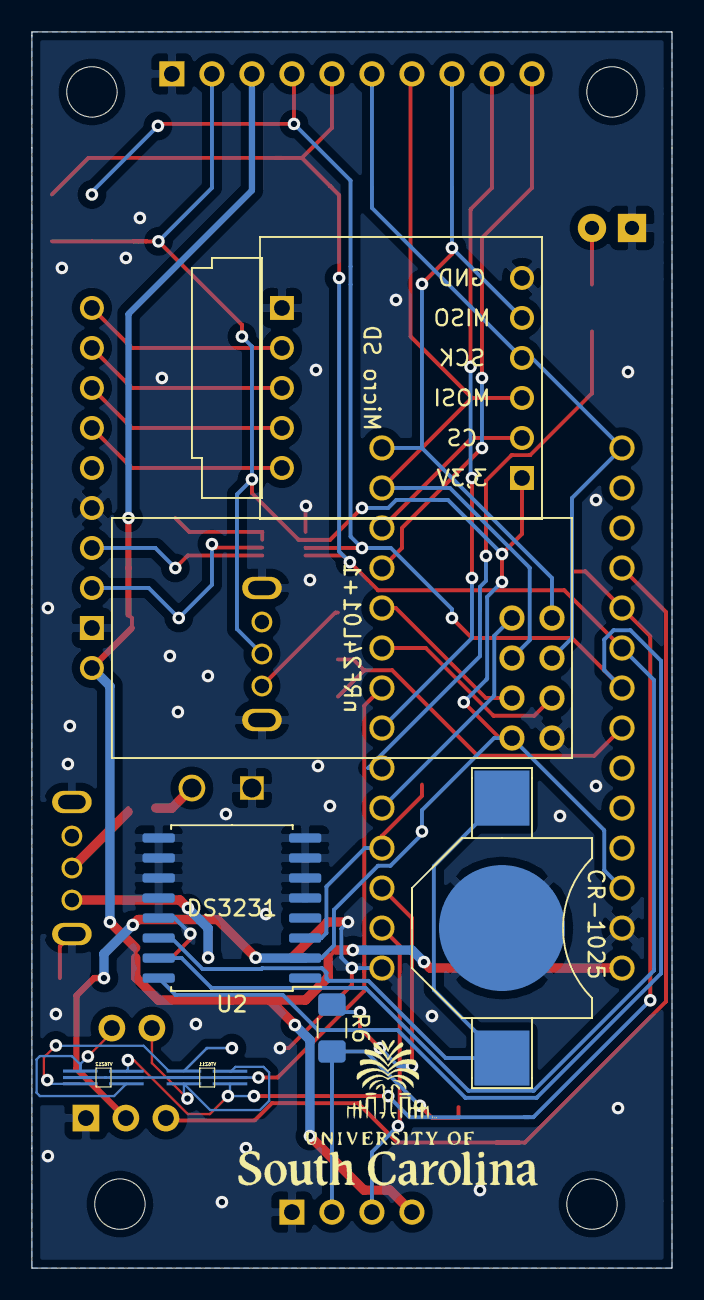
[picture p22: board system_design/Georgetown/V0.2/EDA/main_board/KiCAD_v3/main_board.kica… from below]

Board: 2 copper layers, 40.6 x 78.5 mm, 35 parts (3 on the bottom side), 39 nets.

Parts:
3.3V, 5V: KA78M05_TO252; SOT-223-3_TabPin2
ADS1115: ADS1115
C1: C; R_1206_3216Metric
CR-1025: Battery_Cell; battery_holder_10mm
D1: LED; LED_D3.0mm
F1: Fuse; R_0603_1608Metric_Pad1.05x0.95mm_HandSolder
LiPo Balancing: ADS_Conn
Micro SD: small_microSD
PCA9306: PCA9306
Power: XP60PW; XT60PW
R1, R12: 1k; R_1206_3216Metric_Pad1.42x1.75mm_HandSolder
R2, R3, R8, R10, R11: 4.7k; R_1206_3216Metric_Pad1.42x1.75mm_HandSolder
R4, R5: R; R_1206_3216Metric_Pad1.42x1.75mm_HandSolder
R6: 4.4k; R_1206_3216Metric_Pad1.42x1.75mm_HandSolder
R7: 4.1k; R_1206_3216Metric_Pad1.42x1.75mm_HandSolder
R9: 200; R_1206_3216Metric_Pad1.42x1.75mm_HandSolder
R13: 10k; R_1206_3216Metric_Pad1.42x1.75mm_HandSolder
TDS: tds_3pin; PinHeader_1x03_P2.54mm_Vertical
Teensy 4.0: Teensy4.0; teensy4.0
U2: DS3231M; SOIC-16W_7.5x10.3mm_P1.27mm
VT6Z11, VT6Z12: VT6Z1
Water Height: HCSR04
nRF24L01+1: nRF24L01+
rain gauge: rg_2pin; PinHeader_1x02_P2.54mm_Vertical
switch: grounded_switch
switch2: grounded_switch-whs5-rescue; grounded_switch
top_rail1: top_rail

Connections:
GND: 3.3V.2, 5V.2, ADS1115.6, ADS1115.9, C1.2, CR-1025.2, D1.1, LiPo Balancing.1, Micro SD.6, PCA9306.1, Power.1, R4.2, R7.1, R13.2, TDS.3, Teensy 4.0.1, Teensy 4.0.32, U2.5, U2.6, U2.7, U2.8, U2.9, U2.10, U2.11, U2.12, U2.13, Water Height.1, nRF24L01+1.5, switch.4, switch.5, switch2.4, switch2.5, top_rail1.9
unnamed: CR-1025.1, U2.14
unnamed: 3.3V.3, C1.1, Micro SD.1, PCA9306.2, R2.1, R3.1, R8.1, TDS.2, Teensy 4.0.31, U2.2, nRF24L01+1.1, switch2.2, top_rail1.8
unnamed: D1.2, R1.2
unnamed: F1.1, Power.2
unnamed: F1.2, switch.2
unnamed: Micro SD.2, Teensy 4.0.12
unnamed: Micro SD.3, Teensy 4.0.13, nRF24L01+1.3, top_rail1.3
unnamed: Micro SD.4, Teensy 4.0.20, nRF24L01+1.7, top_rail1.4
unnamed: Micro SD.5, Teensy 4.0.14, nRF24L01+1.8, top_rail1.2
unnamed: R1.1, Teensy 4.0.6
unnamed: PCA9306.4, R2.2, Teensy 4.0.25, U2.15, top_rail1.5
unnamed: PCA9306.3, R3.2, Teensy 4.0.26, U2.16, top_rail1.6
unnamed: R4.1, Teensy 4.0.24, VT6Z11.4, VT6Z12.6
unnamed: R5.2, VT6Z11.1, VT6Z12.3
unnamed: R6.1, Teensy 4.0.3
unnamed: R6.2, R7.2, Water Height.2
unnamed: R8.2, Teensy 4.0.4, U2.3
unnamed: PCA9306.7, PCA9306.8, R9.2
unnamed: ADS1115.7, PCA9306.5, R10.1
unnamed: 3.3V.1, 5V.3, ADS1115.10, R5.1, R9.1, R10.2, R11.2, Teensy 4.0.33, Water Height.4, top_rail1.7
unnamed: ADS1115.8, PCA9306.6, R11.1
unnamed: R12.1, switch2.1
unnamed: R12.2, R13.1, Teensy 4.0.27
unnamed: TDS.1, Teensy 4.0.23
unnamed: Teensy 4.0.2, Water Height.3
unnamed: Teensy 4.0.5, nRF24L01+1.4
unnamed: Teensy 4.0.7, top_rail1.1
unnamed: Teensy 4.0.8, VT6Z11.2, VT6Z11.5, VT6Z12.2, VT6Z12.5
unnamed: Teensy 4.0.9, nRF24L01+1.6
unnamed: Teensy 4.0.10, nRF24L01+1.2
unnamed: Teensy 4.0.11, top_rail1.10
unnamed: ADS1115.1, LiPo Balancing.2
unnamed: ADS1115.2, LiPo Balancing.3
unnamed: ADS1115.3, LiPo Balancing.4
unnamed: ADS1115.4, LiPo Balancing.5
unnamed: 5V.1, switch.1
unnamed: VT6Z11.3, VT6Z11.6, rain gauge.1
unnamed: VT6Z12.1, VT6Z12.4, rain gauge.2

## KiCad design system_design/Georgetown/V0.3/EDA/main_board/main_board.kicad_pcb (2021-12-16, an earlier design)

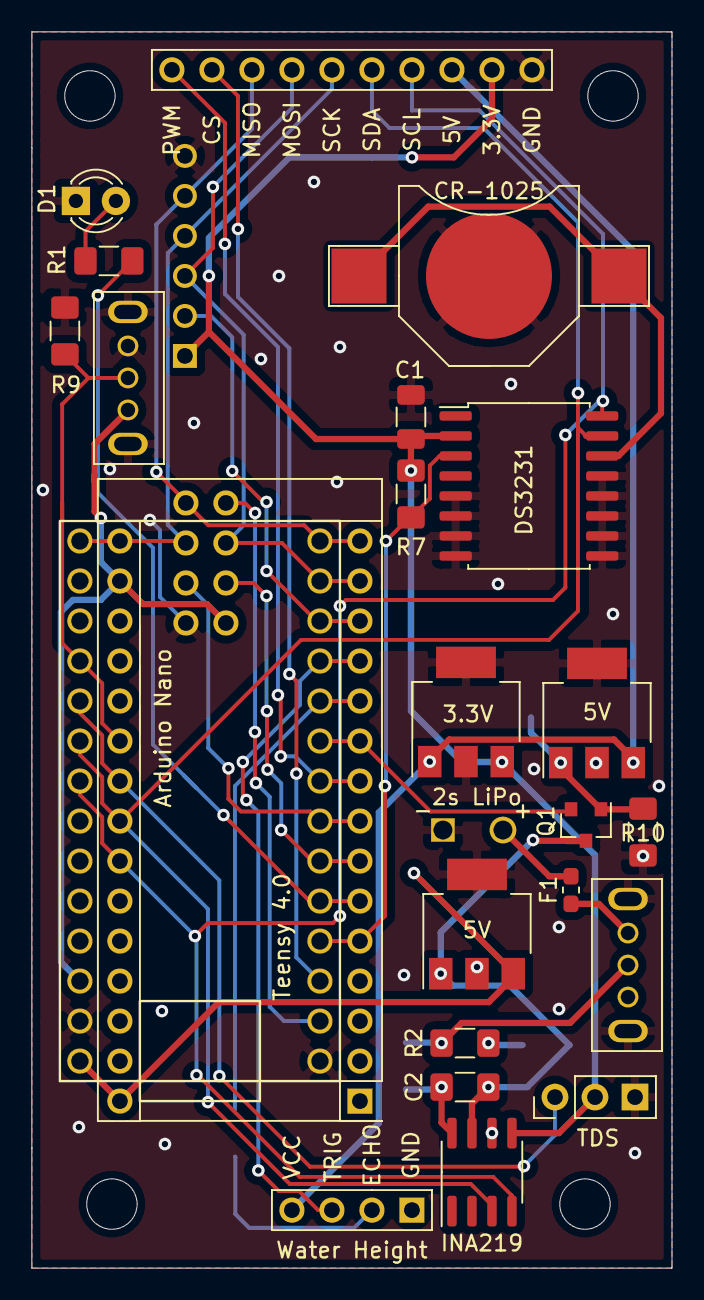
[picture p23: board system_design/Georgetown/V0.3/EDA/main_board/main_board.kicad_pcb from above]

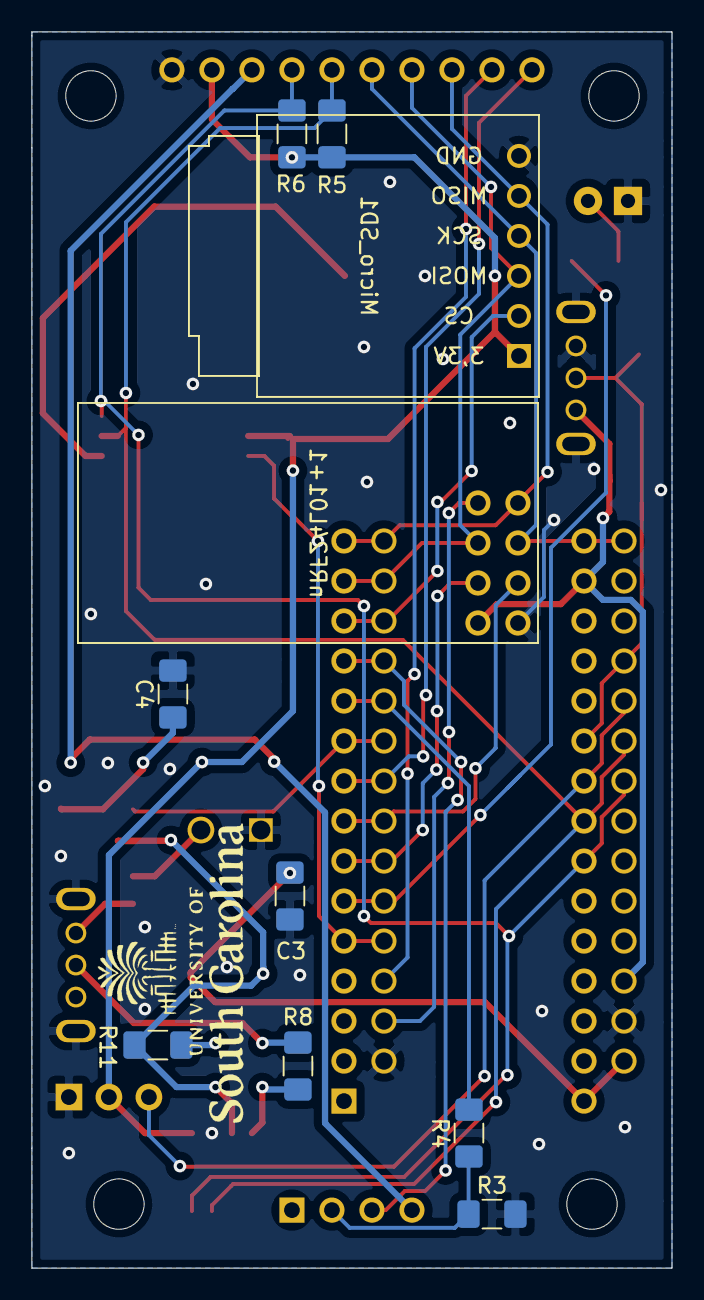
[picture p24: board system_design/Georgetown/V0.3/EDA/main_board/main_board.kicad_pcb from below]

Board: 2 copper layers, 40.6 x 78.5 mm, 34 parts (8 on the bottom side), 33 nets.

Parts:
2s LiPo: XP60PW; XT60PW
3.3V, 5V, 5V#2: KA78M05_TO252; SOT-223-3_TabPin2
Arduino Nano: Arduino_Nano_v2.x-MCU_Module; Arduino_Nano
C1: C; R_1206_3216Metric
C2, C3, C4: C; R_1206_3216Metric_Pad1.42x1.75mm_HandSolder
CR-1025: Battery_Cell; battery_holder_10mm
D1: LED; LED_D3.0mm
DS3231: DS3231M; SOIC-16W_7.5x10.3mm_P1.27mm
F1: Fuse; R_0603_1608Metric_Pad1.05x0.95mm_HandSolder
INA219: INA219AxD; SOIC-8_3.9x4.9mm_P1.27mm
Micro_SD1: small_microSD
Q1: 2N2219; SOT-23
R1: 1k; R_1206_3216Metric_Pad1.42x1.75mm_HandSolder
R2: Rs; R_1206_3216Metric_Pad1.42x1.75mm_HandSolder
R3, R4: 2.2k; R_1206_3216Metric_Pad1.42x1.75mm_HandSolder
R5, R6, R7: 4.7k; R_1206_3216Metric_Pad1.42x1.75mm_HandSolder
R8, R11: 10; R_1206_3216Metric_Pad1.42x1.75mm_HandSolder
R9, R10: 10k; R_1206_3216Metric_Pad1.42x1.75mm_HandSolder
TDS: tds_3pin; PinHeader_1x03_P2.54mm_Vertical
Teensy 4.0: Teensy4.0; teensy4.0
Water Height: HCSR04
nRF24L01+1: nRF24L01+
switch1: grounded_switch
switch2: grounded_DIP_switch; grounded_switch
top_rail1: top_rail

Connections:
GND: 2s LiPo.1, 3.3V.2, 5V.2, 5V#2.2, C1.2, C3.1, C4.2, CR-1025.2, D1.1, DS3231.5, DS3231.6, DS3231.7, DS3231.8, DS3231.9, DS3231.10, DS3231.11, DS3231.12, DS3231.13, INA219.6, Micro_SD1.6, R3.2, R9.2, R10.1, TDS.3, Teensy 4.0.1, Teensy 4.0.32, nRF24L01+1.5, switch1.4, switch1.5, switch2.3, switch2.4, switch2.5, top_rail1.9
unnamed: Arduino Nano.5, DS3231.3, R7.2, Teensy 4.0.4
unnamed: Arduino Nano.6, R1.1, Teensy 4.0.5
unnamed: Arduino Nano.7, Teensy 4.0.6, nRF24L01+1.2
unnamed: Arduino Nano.8, Teensy 4.0.7, nRF24L01+1.6
unnamed: Arduino Nano.9, Teensy 4.0.8, top_rail1.10
unnamed: Arduino Nano.10, Q1.2, Teensy 4.0.9
unnamed: Arduino Nano.11, R4.2, Teensy 4.0.10
unnamed: Arduino Nano.12, Teensy 4.0.11, Water Height.3
unnamed: Arduino Nano.13, Micro_SD1.2, Teensy 4.0.12
unnamed: Arduino Nano.14, Micro_SD1.3, Teensy 4.0.13, nRF24L01+1.3, top_rail1.3
unnamed: Arduino Nano.15, Micro_SD1.5, Teensy 4.0.14, nRF24L01+1.8, top_rail1.2
unnamed: Arduino Nano.16, Micro_SD1.4, Teensy 4.0.20, nRF24L01+1.7, top_rail1.4
unnamed: Arduino Nano.17, Teensy 4.0.31, nRF24L01+1.1, switch2.1
unnamed: Arduino Nano.21, R9.1, Teensy 4.0.23, switch2.2
unnamed: Arduino Nano.22, TDS.1, Teensy 4.0.24
unnamed: Arduino Nano.23, DS3231.15, INA219.3, R5.2, Teensy 4.0.25, top_rail1.5
unnamed: Arduino Nano.24, DS3231.16, INA219.4, R6.2, Teensy 4.0.26, top_rail1.6
unnamed: 5V.3, Arduino Nano.30, C3.2, Teensy 4.0.33
unnamed: CR-1025.1, DS3231.14
unnamed: 3.3V.3, C1.1, DS3231.2, INA219.5, Micro_SD1.1, R5.1, R6.1, R7.1, TDS.2, top_rail1.8
unnamed: C2.1, INA219.8, R8.1
unnamed: 5V.1, C2.2, INA219.7, Q1.3, R11.1
unnamed: 5V#2.1, C4.1, Q1.1, R10.2
unnamed: D1.2, R1.2
unnamed: F1.1, switch1.1
unnamed: 2s LiPo.2, F1.2
unnamed: R2.1, R8.2, switch1.2
unnamed: R3.1, R4.1, Water Height.2
unnamed: R2.2, R11.2
unnamed: Teensy 4.0.2, nRF24L01+1.4
unnamed: Teensy 4.0.3, top_rail1.1
unnamed: 3.3V.1, 5V#2.3, Water Height.4, top_rail1.7

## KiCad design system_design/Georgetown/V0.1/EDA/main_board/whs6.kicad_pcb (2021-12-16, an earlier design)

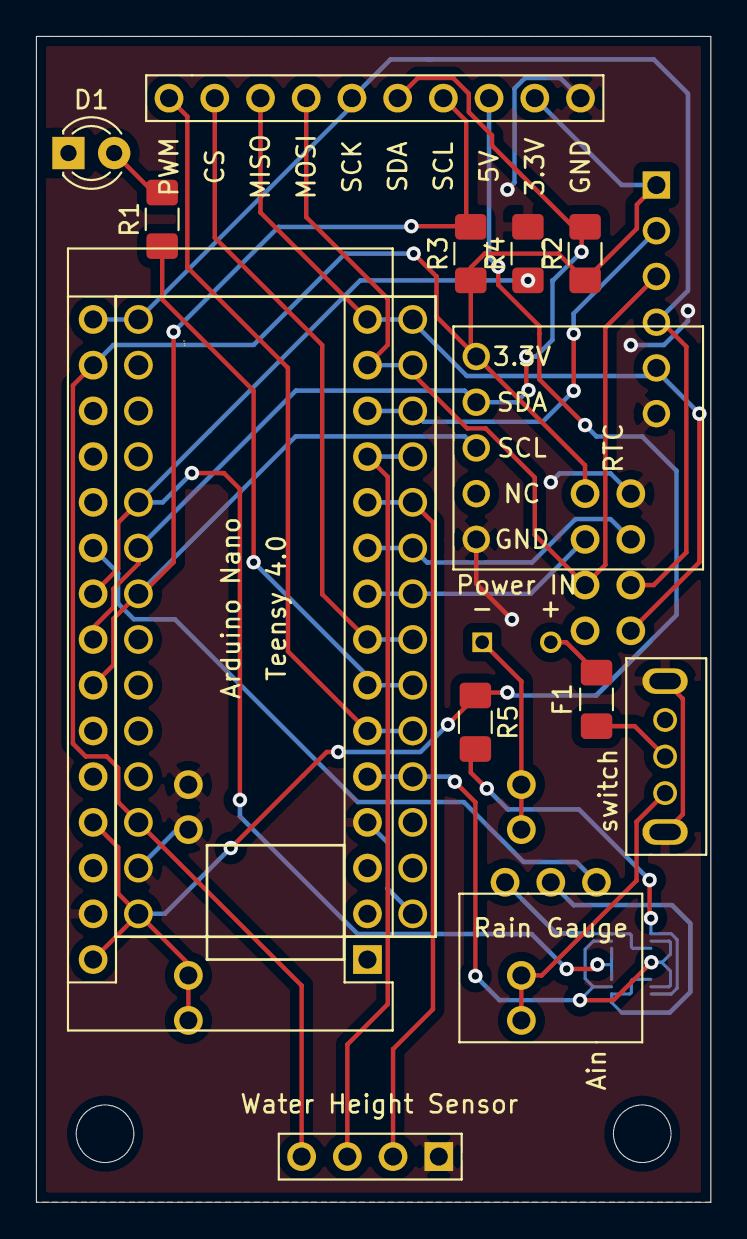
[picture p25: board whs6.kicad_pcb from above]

Board: 2 copper layers, 37.5 x 64.8 mm, 20 parts (0 on the bottom side), 27 nets.

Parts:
Arduino Nano: Arduino_Nano_v2.x; Arduino_Nano
D1: LED; LED_D3.0mm
F1: Fuse; R_1206_3216Metric_Pad1.42x1.75mm_HandSolder
MP1584: MP1584; MP1584_back
Micro SD: small_microSD
Power IN: XP60PW; XT60PW
R1: 1k; R_1206_3216Metric_Pad1.42x1.75mm_HandSolder
R2, R3: 4.7k; R_1206_3216Metric_Pad1.42x1.75mm_HandSolder
R4, R5: R; R_1206_3216Metric_Pad1.42x1.75mm_HandSolder
RTC: small_DS3231
Rain Gauge: rain_gauge-whs5-rescue; Rainfall_sensor
Teensy 4.0: Teensy4.0; teensy4.0
Ultrasonic_sensor1: HCSR04
VT6Z11, VT6Z12: VT6Z1
nRF24L01+: nRF24L01+
switch: grounded_switch
top_rail1: top_rail

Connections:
GND: Arduino Nano.4, Arduino Nano.29, D1.1, MP1584.7, MP1584.8, Micro SD.6, R4.2, RTC.1, Teensy 4.0.1, Teensy 4.0.32, Ultrasonic_sensor1.1, nRF24L01+.5, switch.4, switch.5, top_rail1.9
unnamed: Arduino Nano.5, Teensy 4.0.4, VT6Z11.2, VT6Z11.5, VT6Z12.2, VT6Z12.5
unnamed: Arduino Nano.6, Teensy 4.0.5, top_rail1.10
unnamed: Arduino Nano.7, R1.1, Teensy 4.0.6
unnamed: Arduino Nano.8, Teensy 4.0.7, top_rail1.1
unnamed: Arduino Nano.9, Teensy 4.0.8, nRF24L01+.2
unnamed: Arduino Nano.10, Teensy 4.0.9, nRF24L01+.6
unnamed: Arduino Nano.11, Teensy 4.0.10, Ultrasonic_sensor1.2
unnamed: Arduino Nano.12, Teensy 4.0.11, Ultrasonic_sensor1.3
unnamed: Arduino Nano.13, Micro SD.2, Teensy 4.0.12
unnamed: Arduino Nano.14, Micro SD.3, Teensy 4.0.13, nRF24L01+.3, top_rail1.3
unnamed: Arduino Nano.15, Micro SD.5, Teensy 4.0.14, nRF24L01+.8, top_rail1.2
unnamed: Arduino Nano.16, Micro SD.4, Teensy 4.0.20, nRF24L01+.7, top_rail1.4
unnamed: Arduino Nano.17, Micro SD.1, R2.1, R3.1, RTC.5, Teensy 4.0.31, Ultrasonic_sensor1.4, nRF24L01+.1, top_rail1.8
unnamed: Arduino Nano.21, Rain Gauge.3
unnamed: Arduino Nano.22, R4.1, Teensy 4.0.24, VT6Z11.4, VT6Z12.6
unnamed: Arduino Nano.23, R2.2, RTC.4, Teensy 4.0.25, top_rail1.5
unnamed: Arduino Nano.24, R3.2, RTC.3, Teensy 4.0.26, top_rail1.6
unnamed: Arduino Nano.27, Arduino Nano.30, MP1584.5, MP1584.6, R5.1, Teensy 4.0.33, top_rail1.7
unnamed: D1.2, R1.2
unnamed: F1.1, Power IN.2
unnamed: F1.2, switch.2
unnamed: MP1584.3, MP1584.4, Power IN.1
unnamed: R5.2, VT6Z11.1, VT6Z12.3
unnamed: MP1584.1, MP1584.2, switch.1
unnamed: Rain Gauge.1, VT6Z11.3, VT6Z11.6
unnamed: Rain Gauge.2, VT6Z12.1, VT6Z12.4

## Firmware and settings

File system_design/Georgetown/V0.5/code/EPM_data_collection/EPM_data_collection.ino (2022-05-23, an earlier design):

/*
 * This code is to be uploaded to the base package or solar package. The EPM package uses EPM_data_collection.ino. 
 * This is the sketch that will run during deployment and take stage, temperature, pressure, humidity, and power
 * measurements. The data is saved on an SD card and collection occurs every five minutes as dictated by RTC alarms.
 * 
 * Written by Corinne Smith
 * July 9 2021
 * Modified from ArduinoGetStarted, www.ArduinoGetStarted.com
 * Modified from Dejan Nedelkowski, www.HowToMechatronics.com
 * Modified from ArduinoLearning, www.ArduinoLearning.com
*/

#include <SD.h>                         // for SD card module
#include <SPI.h>                        // for SPI
#include <Wire.h>                       // for I2C
#include <HCSR04.h>                     // for the USS
#include <DS3232RTC.h>                  // for the RTC https://github.com/JChristensen/DS3232RTC
#include <nRF24L01.h>                   // for the nRF24L01
#include <RF24.h>                       // for the nRF24L01
#include <avr/sleep.h>                  // for sleep mode
#include <Adafruit_Sensor.h>            // for BME 
#include <Adafruit_BME280.h>            // for BME
#include <Adafruit_INA219.h>            // for voltage monitor

const int RTCinterrupt = 2;             // RTC interrupt from sleep mode on digital pin 2 (INT_0)
const int nRFinterrupt = 3;             // nRF interrupt from sleep mode on digital pin 3 (INT_1)
#define SEALEVELPRESSURE_HPA (1013.25)  // constant for bme

// nRF24L01 -------------------------------------------------------------------------------------------
RF24 radio(7, 6); // CE, CSN
const byte addresses [][6] = {"00001", "00002", "00003", "00004"};  //Setting the two addresses. One for transmitting and one for receiving
int command = 0;      
int PC = 4;
int MAG = 5;
boolean mag_on = false;
boolean paired = false;
boolean just_set = false;
bool mag_msg = false;

//HC-SR04 ----------------------------------------------------------------------------------------------
const int trigPin = 9;     
const int echoPin = 8;      
UltraSonicDistanceSensor distanceSensor(trigPin, echoPin);

//SD ---------------------------------------------------------------------------------------------------
const int pinCS = 10;

//BME280 -----------------------------------------------------------------------------------------------
Adafruit_BME280 bme;

//INA219 -----------------------------------------------------------------------------------------------
Adafruit_INA219 ina219;

//controls ---------------------------------------------------------------------------------------------
const int LED = A3;
const int time_interval = 5;          // interval in which the minutes will be delayed. Default is five minutes
unsigned long prevTimeElapsed = 0;

void setup() {
  Serial.begin(9600);
  pinMode(pinCS, OUTPUT);
  pinMode(LED, OUTPUT);
  pinMode(trigPin, OUTPUT);
  pinMode(echoPin, INPUT);
  pinMode(PC, OUTPUT);
  pinMode(MAG, OUTPUT);
  pinMode(RTCinterrupt, INPUT_PULLUP);            // configure the interrupt pin using the built-in pullup resistor
  Serial.println("Executing EPM_data_collection.ino");

  // SD card initialization --------------------------------------------------------------------------------------------------------------------------
  if (!SD.begin())                               
  {
    digitalWrite(LED, HIGH);                      // LED remains on if SD card does not work
    Serial.println("no SD found");
    while (1);                                    
  }
  else
  {
    Serial.println("SD found");
  }

  // nRF24L01 initialization -------------------------------------------------------------------------------------------------------------------------
  radio.begin();                            
  radio.openWritingPipe(addresses[0]);            // set the address at which we will send the data (the rf controller's address)
  radio.openReadingPipe(1, addresses[1]);         // set the address at which we will receive the data. Change this if deploying multiple packages to
                                                  //   give each package a unique address
  radio.setPALevel(RF24_PA_MAX);                  // can set as minimum or maximum depending on the distance between the rf controller and package

  // RTC initializaiton ------------------------------------------------------------------------------------------------------------------------------
  RTC.begin();
  
  // initialize the alarms, clear the alarm flags, clear the alarm interrupts
  RTC.setAlarm(ALM1_MATCH_DATE, 0, 0, 0, 1);
  RTC.setAlarm(ALM2_MATCH_DATE, 0, 0, 0, 1);
  RTC.alarm(ALARM_1);
  RTC.alarm(ALARM_2);
  RTC.alarmInterrupt(ALARM_1, false);
  RTC.alarmInterrupt(ALARM_2, false);
  RTC.squareWave(SQWAVE_NONE);
  
  // get the current time from the RTC and set an alarm according to the time interval
  time_t t;                               
  t = RTC.get();                            
  
//  // uncomment to set the time interval units to seconds
//  if(second(t)< 60 - time_interval){
//    RTC.setAlarm(ALM1_MATCH_SECONDS , second(t)+time_interval, 0, 0, 0);
//  }
//  else {
//    RTC.setAlarm(ALM1_MATCH_SECONDS , second(t)-60+time_interval, 0, 0, 0);
//  }
  
  // uncomment to set the time interval units to minutes
  if (minute(t) < 60 - time_interval) {
    RTC.setAlarm(ALM1_MATCH_MINUTES , 0, minute(t) + time_interval, 0, 0);
  }
  else {
    RTC.setAlarm(ALM1_MATCH_MINUTES , 0, minute(t) - 60 + time_interval, 0, 0);
  }

  // clear the alarm flag and configure the interrupt operation
  RTC.alarm(ALARM_1);
  RTC.squareWave(SQWAVE_NONE);
  RTC.alarmInterrupt(ALARM_1, true);

  // BME initialization ------------------------------------------------------------------------------------------------------------------------------
  bme.begin(0x76);

  // Voltage regulator initialization -----------------------------------------------------------------------------------------------------------------
  uint32_t currentFrequency;
  ina219.begin();
}

void loop() {
  digitalWrite(LED, LOW);     // turn off LED before sleeping
  digitalWrite(PC, LOW);      // make sure magnet control circuit is off
  radio.startListening();     // set nRF24L01 as receiver
  delay(10);
  goSleep();
}

void goSleep() {
  Serial.println("Going to sleep...");
  delay(100);

  // initialize just_set as false. If we get a pairing command it will become true
  just_set = false;
  delay(100);

  // activate sleep mode, attach interrupt and assign a waking function to run
  sleep_enable();                               
  attachInterrupt(digitalPinToInterrupt(RTCinterrupt), RTCtrigger, LOW);
  attachInterrupt(digitalPinToInterrupt(nRFinterrupt), nRFtrigger, LOW);
  set_sleep_mode(SLEEP_MODE_PWR_DOWN);              // set to full sleep mode   
  sleep_cpu();                                  

  // run the magnet toggle function if we received a command other than pairing
  if (mag_msg == true && just_set == false) {
    toggleMag();
  }

  // run the data collection function if RTC alarm goes off or if we have finished reading the nRF message
  if(just_set = false) {
    logData();                                   
  }
  
  // set the next alarm
  time_t t;
  t = RTC.get();
  
//  // uncomment to set the time interval units to seconds
//  if(second(t) < 60 - time_interval){
//    RTC.setAlarm(ALM1_MATCH_SECONDS , second(t)+time_interval, 0, 0, 0);
//  }
//  else {
//    RTC.setAlarm(ALM1_MATCH_SECONDS , second(t)-60+time_interval, 0, 0, 0);
//  }
  
  // uncomment to set the time interval units to minutes
  if (minute(t) < 60 - time_interval) {
    RTC.setAlarm(ALM1_MATCH_MINUTES , 0, minute(t) + time_interval, 0, 0);
  }
  else {
    RTC.setAlarm(ALM1_MATCH_MINUTES , 0, minute(t) - 60 + time_interval, 0, 0);
  }

  // clear the alarm flag
  RTC.alarm(ALARM_1);
}

void RTCtrigger() {
// this is the wake up function to run once the RTC interrupt is fired
  Serial.println("RTC interrupt fired");
  delay(100);
  sleep_disable();                        // disable sleep mode
  detachInterrupt(digitalPinToInterrupt(RTCinterrupt));          // clear the interrupt flag
}

void nRFtrigger() {                             
// this is the wake up function to run once the nRF interrupt is fired
  sleep_disable();
  detachInterrupt(digitalPinToInterrupt(nRFinterrupt));
  delay(2000);
  
  // determines if interrupt was caused by a transmission (tx), transmission failure (fail), or reception (rx)
  bool tx, fail, rx;
  radio.whatHappened(tx, fail, rx);                   

  // if we received a message, read the message and act accordingly
  if ( rx || radio.available()) {                     
    radio.read(&command, sizeof(command)); 
    delay(500);
    // if we got a pairing command:
    if (command == 1) {                                       
      radio.stopListening();
      delay(50);
      radio.write(&command, sizeof(command));     // send back a ping to the transmitter
      delay(50);
      radio.startListening();
      just_set = true;                            // change boolean so magnet is not toggled and data not collected
    }
    // if we got an ON command: 
    if (command == 2) {
      mag_on = true;
    }
    // if we got an OFF command: 
    else if (command == 3) {
      mag_on = false;
    }
    mag_msg = true;           // change boolean so toggleMag() is run (don't want to call within the wakeup function)
  }
}

void toggleMag() {
// this is the function that toggles the EPM

  // if we received an ON command
  if(mag_on == true) {
      digitalWrite(PC, HIGH);          // turn on the magnet control circuit
      delay(1500);
      for (int i = 0; i < 30; i++)     // pulse the PWM pin at 50 Hz
        {
          digitalWrite(MAG, HIGH);
          delay(2);
          digitalWrite(MAG, LOW);
          delay(18);
        }
        Serial.println("Mag on");
        delay(2000);
        digitalWrite(PC, LOW);         // turn off the magnet control circuit
    }

    // if we received an OFF command
    else if(mag_on == false) {
      digitalWrite(PC, HIGH);          // turn on the magnet control circuit
      delay(1500);
      for (int i = 0; i < 30; i++)     // pulse the PWM pin at 33 Hz
        {
          digitalWrite(MAG, HIGH);
          delay(1.5);
          digitalWrite(MAG, LOW);
          delay(19);
        }
        Serial.println("Mag off");
        delay(5000);
        digitalWrite(PC, LOW);         // turn off the magnet control circuit
    }
    mag_msg = false;
}

void logData() {
// this is the data collection function
  unsigned long timeElapsed = millis();
  Serial.println("Recording data...");
  digitalWrite(LED, HIGH);
  delay(10);

  // take five distance readings and average them
  float dist[5];
  float total = 0;
  float num = 0;
  for (int i = 0; i < 5; i++) {
    dist[i] = distanceSensor.measureDistanceCm();
    delay(500);
    if (dist[i] > 0) {
      total = total + dist[i];
      num++;
    }
  }
  float avgDist = total / num;

  // record the ambient temperature, humidity, pressure
  float temp = bme.readTemperature();
  float humidity = bme.readHumidity();
  float pressure = bme.readPressure() / 100.0F;
  delay(50);

  // record the voltage, current, and power draw from the LiPo
  float busvoltage = ina219.getBusVoltage_V();
  float current_mA = ina219.getCurrent_mA();
  float power_mW = ina219.getPower_mW();

  // print the data to the file that will be saved on the SD card
  File myFile = SD.open("001.csv", FILE_WRITE);    // change to the file name you want to store the data

  if (myFile)                             // tests if the file has opened
  {
    // write the RTC data
    time_t t = RTC.get();
    myFile.print(String(month(t)));
    myFile.print("/");
    myFile.print(String(day(t)));
    myFile.print("/");
    myFile.print(String(year(t)));
    myFile.print(" ");
    myFile.print(String(hour(t)));
    myFile.print(":");
    myFile.print(String(minute(t)));
    myFile.print(":");
    myFile.print(String(second(t)));
    myFile.print(" ");

    // write the USS data
    for (int i = 0; i < 5; i++) {
      myFile.print(dist[i]); myFile.print(" ");
    }
    myFile.print(avgDist); myFile.print(" ");

    // write the BME data
    myFile.print(temp); myFile.print(" ");
    myFile.print(humidity); myFile.print(" ");
    myFile.print(pressure); myFile.print(" ");

    // write the power data
    myFile.print(busvoltage); myFile.print(" ");
    myFile.print(current_mA); myFile.print(" ");
    myFile.print(power_mW); myFile.print(" ");

    myFile.println("");
    myFile.close();           // closes and saves the file to the SD card
    Serial.print("Complete! Elapsed time: "); Serial.print(timeElapsed - prevTimeElapsed); Serial.println(" ms");
    prevTimeElapsed = timeElapsed;
  }
  else
  {
    Serial.println("Error opening file");
    digitalWrite(LED, HIGH);                // LED will stay on if the file is not opening properly. 
    while (1);
  }
  delay(100);
  digitalWrite(LED, LOW);
}

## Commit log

2021-12-16 moving things around
    [Magdron mount.kicad_pcb, Magdron mount.sch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]
2021-12-29 add CAD files
    [EPM_housing.stl, base_sensor_plate.stl, controller_v1.kicad_pcb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]
2022-01-20 refill PCB zones
    [main_board.kicad_pcb]
2022-02-10 update most recent footprints
2022-02-12 major cleanup
    [ARTS_v3_fieldtest_jan15.csv, Magdron mount.kicad_pcb, Magdron mount.sch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]
2022-02-16 update interrupt pin syntax
2022-02-18 add figure data
    [USGS_aug18.csv, v4_lab_test_feb23.CSV, v4_lab_test_feb23.xlsx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]
2022-02-19 add bill of materials
2022-02-19 modify serial printed sketch name
2022-02-19 add f3d files
    [EPM_housing.f3d, base_plate.f3d, sensor_housing.f3d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]
2022-05-23 change SD file name, fix mag_msg issue
    [EPM_data_collection.ino]
2022-05-31 update all figures
    [USGS_aug18.csv, v4_lab_test_feb23.CSV, v4_lab_test_feb23.xlsx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]
2025-02-06 added variations
    [ARTS_v3_fieldtest_jan15.csv, EPM_housing.f3d, EPM_housing.stl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]
2025-02-24 New Sensor Housing Design
    [sensor_housing 3.0 v1.f3d]
2025-02-26 V0.5 added
    [Magdron mount.kicad_pcb, Magdron mount.sch, controller_v1.kicad_pcb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]
2025-02-27 updated to latest KiCAD version
2025-02-28 Update BOM
2026-06-16 OS 0.5.2 added
    [bill_of_materials.xlsx, main_board.kicad_sch]
2026-06-17 added a .0 to a major version number.
    [ANSI (in).dwg, ANSI (in).idw, ANSI (mm).dwg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]
